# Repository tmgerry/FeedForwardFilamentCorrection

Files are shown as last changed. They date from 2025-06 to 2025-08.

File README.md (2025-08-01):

# Colorado State University - Prawel Lab

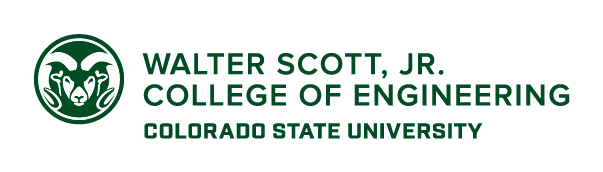
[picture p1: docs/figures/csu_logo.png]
csu logo


# Feed Forward Filament Diameter Correction

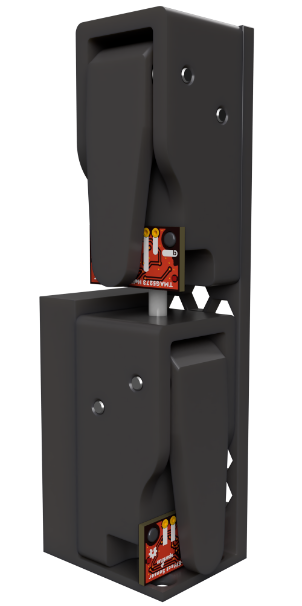
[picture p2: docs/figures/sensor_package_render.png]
diameter sensor render
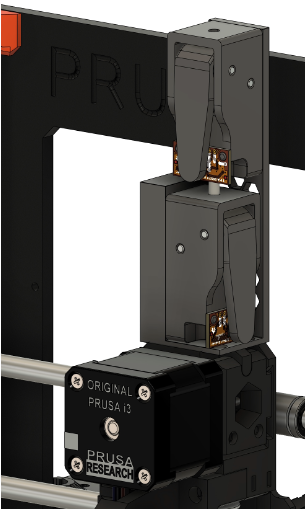
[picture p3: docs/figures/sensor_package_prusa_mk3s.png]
diameter sensor render
 

## Software Installation Instructions - 

These instructions assume you have used [Klipper Installation And Update Helper](https://github.com/dw-0/kiauh) to install klipper.

1. Clone the repository -
```
git clone https://github.com/tmgerry/FeedForwardFilamentCorrection.git
```

1. Run the install tool and restart klipper - 
```
cd && cd CSU-in-situ/ && python3 klippy/installer.py && cd && sudo service klipper restart
```

1. Configure secondary MCU and add to config based on the example configuration file.

1. Put that file in the same folder as your `printer.cfg` file.

1. Include a line like the following at the top of your existing `printer.cfg` file to activate the diameter sensor. This requires hardware and config file to be setup correctly or klipper will not start.

```
[include diameter_sensor.cfg] # Comment out if no diameter sensor is connected to disable.
```

## Microcontroller Firmware Installation

This klipper add on requires a secondary microcontroller to communicate with the magnetic sensors over I2C. This microcontroller requires klipper firmware to be installed. Other microcontrollers, (especially Sparkfun QWIIC or Adafruit Stemma QT boards, which allow for solder free wiring) are most likely compatible assuming there is a klipper firmware build compatible with the specific chip they use. The Sparkfun RP2040 Pro Micro has been extensively tested and validated to be compatible.

### Adafruit and Sparkfun RP2040 Dev Boards

Sparkfun RP2040 Pro Micro

Adafruit and Sparkfun use a different flash chip on their boards so the procedure will be the same as standard Raspberry Pi Picos except for minor setting changes in the config, and the fact that most of their boards have individual reset and boot-sel buttons.

1. Open terminal on raspberry pi with klipper installed
1. run in shell `cd klipper`
1. run in shell `make clean`
1. run in shell `make menuconfig` and the config menu will open, set the following options
   1. microcontroller architecture `Raspberry Pi RP2040`
   1. No bootloader offset
   1. Flash Chip - `GENERIC_03H with CLKDIV 4`
   1. Communication Interface - `USBSERIAL`
1. Press `Q` to save and exit
1. run in shell `make`, a bunch of lines saying "Compiling out/src......" will appear.
1. At the end you should see a line saying `Creating uf2 file out/klipper.uf2` This is the firmware file we want to upload to the pi.
1. Copy the file from above, to your computer. SFTP is convenient and easy for this.
1. Plug in the microcontroller to your computer while holding down the reset button, a removable usb-drive should appear in your file browser.
1. Drag the `klipper.uf2` file onto the picos removable drive, it will quickly disappear and restart.
1. Firmware is now flashed and the pico is ready to be used in klipper.

# Hardware

The sensor is based on the [InFiDEL Filament Diameter Sensor](https://www.printables.com/model/57154-infidel-inline-filament-diameter-estimator-lowcost), with modifications to improve accuracy and precision, as well as compatibility with TMAG5273 Hall Effect Sensor.

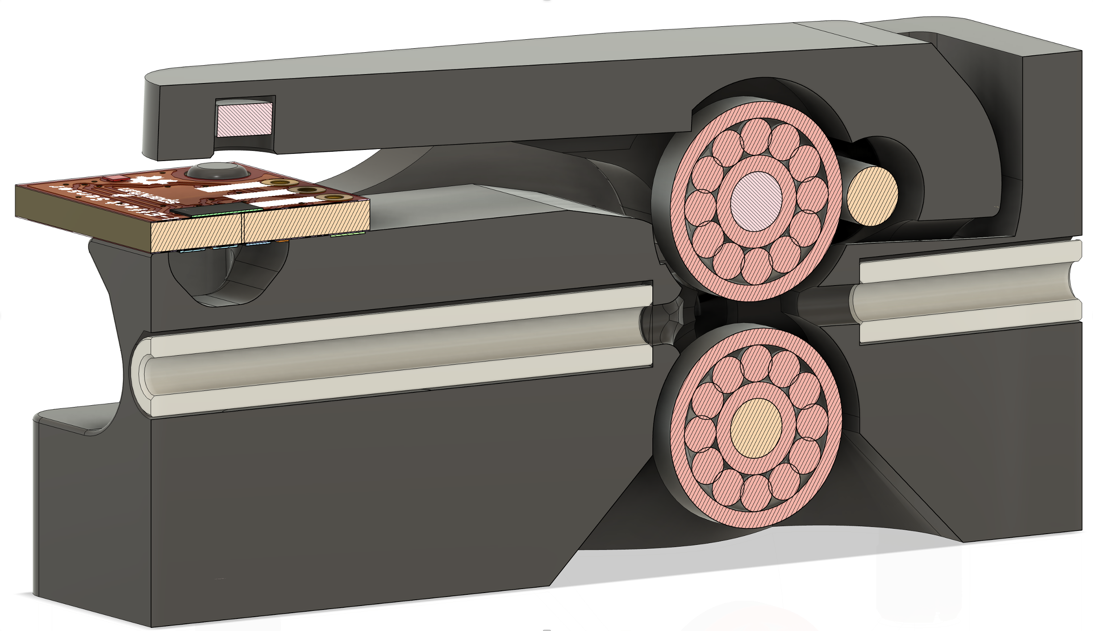
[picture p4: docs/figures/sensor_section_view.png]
sensor_section_view


## Printed Parts

There are two printed parts in this sensor, they can be printed on a standard FDM Printer, but a resin printer yields higher precision parts. We print our sensors with Formlabs Tough 1500, but stiffer materials will likely yield even better results.

The two included .STL files in the CAD folder are the ones that need to be printed.

## General BOM

* 1x Sparkfun Pro Micro RP2040 ([Sparkfun](https://www.sparkfun.com/sparkfun-pro-micro-rp2040.html))
* 1x Sparkfun QWIIC Cable Set ([Sparkfun](https://www.sparkfun.com/sparkfun-qwiic-cable-kit.html))
* Superglue for attaching the TMAG sensor.

## Sensor BOM

* (1x) Sparkfun Mini Linear 3D Hall-Effect Sensor TMAG5273 ([Sparkfun](https://www.sparkfun.com/sparkfun-mini-linear-3d-hall-effect-sensor-tmag5273-qwiic.html))
* (1x) Spring ([McMASTER-CARR](https://www.mcmaster.com/9657K629/)) *similar springs can be sourced from other vendors but we have found them to be of unreliable stiffness*
* (1x) Magnet ([McMASTER-CARR](https://www.mcmaster.com/5862K138/)) *sensor geometry is finely tuned to magnet strength, ordering this specific part is highly advised.*
* (1x) Undersized 3mm Dowel Pin 16mm Long ([McMASTER-CARR](https://www.mcmaster.com/97049A329/)) *recommend McMASTER but can be sourced other places, ensure undersized to allow for easy assembly*
* (2x) Undersized 3mm Dowel Pin 25mm Long ([Amazon](https://www.amazon.com/uxcell-Stainless-Support-Fasten-Elements/dp/B07M63LMCM?s=industrial)) *Pins in this size were harder to source, Pins from Amazon worked fine but some were not within tolerance and could not be used. They can be ordered from misumi but costs significantly more.*
* (4x) 3mmx10mmx4mm Bearings ([Amazon](https://www.amazon.com/dp/B07FW389P1?_encoding=UTF8&ref_=cm_sw_r_ud_dp_GC7XPF5W3NQKGKW1RP3B&th=1))
* (1x) M6 x 1mm Thread, 8mm Long Set Screw ([McMASTER-CARR](https://www.mcmaster.com/92605A127/))
* (4x) M3 Screw to Expand Inserts. ([McMASTER-CARR](https://www.mcmaster.com/94510A030/)) *for rear sensor mounting holes, only necesarry if there is frequent assembly/dissassembly*
* Calibration Hardware

## Sensor Calibration

The filament diameter sensor can only be as accurate as it's calibration. We use a 3 point calibration with the pin gauges featured below to calibrate the sensor, a more extensive calibration could be done with four, five, or even 6+ pins to make it more precise but 3 was chosen by our team to have the optimal balance of cost, time, and accuracy.

### Calibration Gauges

* (1x) 0.0665 Class Z No Go Gauge ([McMASTER-CARR](https://www.mcmaster.com/23065A674-23065A305/))
* (1x) 0.0690 Class Z No Go Gauge ([McMASTER-CARR](https://www.mcmaster.com/23065A674-23065A069/))
* (1x) 0.0710 Class Z No Go Gauge ([McMASTER-CARR](https://www.mcmaster.com/23065A674-23065A071/))

### Calibration Procedure

1. Using the microcontroller selected above - flash the calibration firmware using the inlcuded arduino sketch.
   1. Ensure to set the i2c address at the top of the file to the appropriate sensor if using a dual sensor configuration.
1. Place calibration gauge into sensor from the TMAG side
1. Open Arduino serial console and clear output
1. Log as many values as you want and store in a spreadsheet
1. Repeat for each calibration pin you have.
1. Run a linear regression on the samples you collected to get the correct calibration values to input into your config file.

# Klipper Configuration
[Example configuration available here](config_examples/diameter_sensor_example.cfg)

# More Info

### How extrusion is changed -

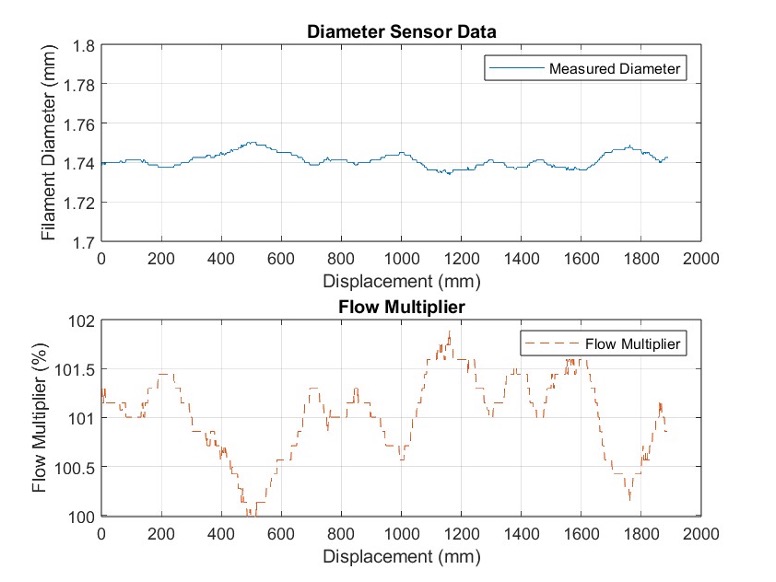
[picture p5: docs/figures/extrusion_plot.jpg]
extrusion plot

*Simple plot showing how changes in filament diameter change the klipper extrusion multiplier*

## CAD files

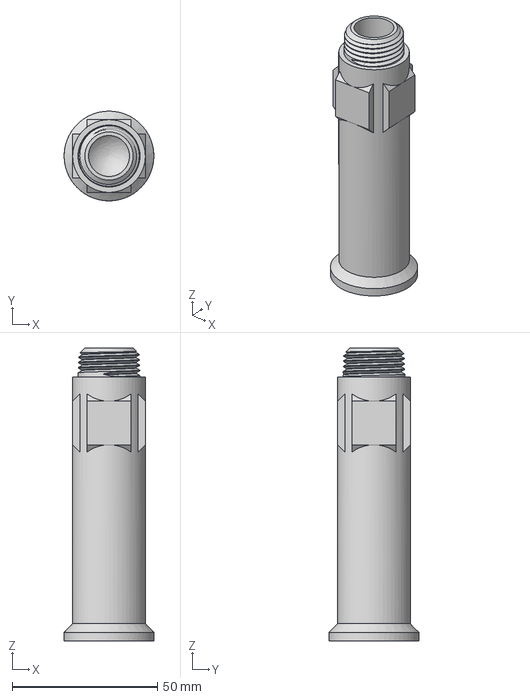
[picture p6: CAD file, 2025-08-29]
CAD/pressure_tube/tube_042.step
30.9 x 30.9 x 100.8 mm

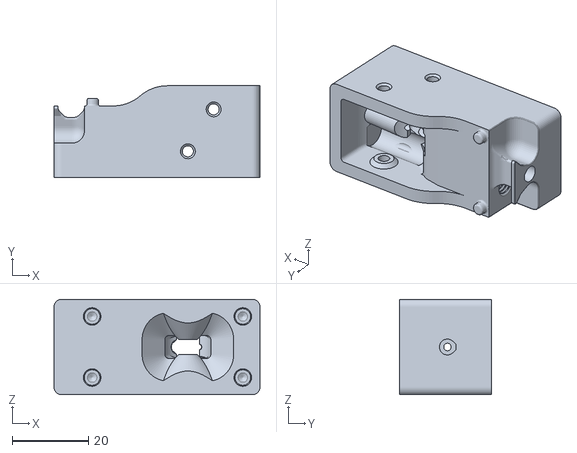
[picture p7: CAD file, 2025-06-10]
CAD/Sensor_Body.stl
54.0 x 24.0 x 25.0

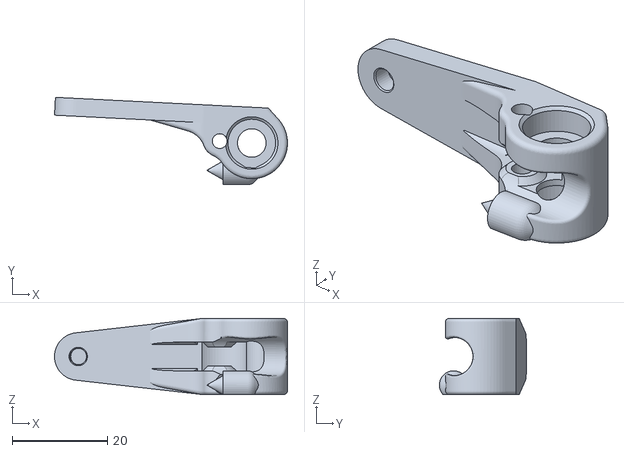
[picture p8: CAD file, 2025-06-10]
CAD/Lever.stl
48.9 x 18.3 x 16.0

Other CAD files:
CAD/Filament Diameter Sensor.f3d

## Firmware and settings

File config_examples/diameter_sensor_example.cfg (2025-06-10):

# Include the following line in your printer.cfg file
#
# [include diameter_sensor.cfg] # comment out if no diameter sensor is connected
# 

[mcu diameter_sensor_mcu]
serial: /dev/serial/by-id/usb-Klipper_rp2040..............

[tmag5273_filament_width_sensor]
i2c_mcu: diameter_sensor_mcu
i2c_bus: i2c0e
i2c_speed: 100000
# Calibration
cal_slope_1: -1.385324e-05  # Sensor 0
cal_intercept_1: 2.069541   # Sensor 0	

cal_slope_2: -1.374351e-05  # Sensor 1
cal_intercept_2: 2.067393   # Sensor 1

#   The nominal filament diameter. This parameter must be provided.
default_nominal_filament_diameter: 1.75
max_difference: 100
#   Maximum allowed filament diameter difference in millimeters (mm).
#   If difference between nominal filament diameter and sensor output
#   is more than +- max_difference, extrusion multiplier is set back
#   to %100. The default is 0.200.
measurement_delay_1: 147.5
measurement_delay_2: 203
#   The distance from sensor to the melting chamber/hot-end in
#   millimeters (mm). The filament between the sensor and the hot-end
#   will be treated as the default_nominal_filament_diameter.
enable: False
#   Sensor enabled or disabled after power on. The default is to
#   disable.
# measurement_interval: 2
#   The approximate distance (in mm) between sensor readings. The
#   default is 2mm.
# logging: True
#   Out diameter to terminal and klipper.log can be turn on|of by
#   command.
min_diameter: 0
#   Minimal diameter for trigger virtual filament_switch_sensor.
max_diameter: 100
#   Maximum diameter for triggering virtual filament_switch_sensor.
#   The default is default_nominal_filament_diameter + max_difference.
use_current_dia_while_delay: False
#   Use the current diameter instead of the nominal diameter while
#   the measurement delay has not run through.
average_mode: 5
z_axis_range_80mT: False
xy_axis_range_80mT: False
super_sampling: 75
mag_temp_mode: 0
dual_sensor: True


[temperature_sensor diameter_sensor_CPU]
sensor_type: temperature_mcu
sensor_mcu: diameter_sensor_mcu
min_temp: -10
max_temp: 100


[temperature_sensor diameter_sensor_1]
sensor_type: TMAG5273_TEMP
tmag_poll_time: 1
sensor_number: 1

[temperature_sensor diameter_sensor_2]
sensor_type: TMAG5273_TEMP
tmag_poll_time: 1
sensor_number: 2



[gcode_macro disable_filament_correction]
gcode:
    M221 S10
    DISABLE_FILAMENT_WIDTH_SENSOR
    RESET_FILAMENT_WIDTH_SENSOR
    SET_LED LED=sensor_status RED=1 GREEN=0 BLUE=0

[gcode_macro enable_filament_correction]
gcode:
   ENABLE_FILAMENT_WIDTH_SENSOR
   SET_LED LED=sensor_status RED=0 GREEN=1 BLUE=1

[gcode_macro get_filament_width]
gcode:
    QUERY_FILAMENT_WIDTH
    QUERY_RAW_FILAMENT_WIDTH

[gcode_macro _reset_filament_width]
gcode:
    RESET_FILAMENT_WIDTH_SENSOR


[gcode_macro get_filament_sensor_temps]
gcode:
    GET_FILAMENT_WIDTH_SENSOR_TEMPS


[gcode_macro get_filament_sensor_debug]
gcode:
  GET_FILAMENT_WIDTH_SENSOR_DEBUG

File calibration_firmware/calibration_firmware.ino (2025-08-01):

#include <Wire.h>      // Used to establish serial communication on the I2C bus
#include "tmag_5273.h" // Used to send and recieve specific information from our sensor

TMAG5273 sensor; // Initialize hall-effect sensor

// I2C default address
// Alternate i2c address comments to switch between sensors when using more than 1 sensor
// uint8_t i2cAddress = 0x78;
uint8_t i2cAddress = 0x22;

int super_sample = 250;
float z_buffer = 0;

void setup() 
{
  Wire.begin();
  // Start serial communication at 115200 baud
  Serial.begin(115200);
  delay(1000);

  // Begin example of the magnetic sensor code (and add whitespace for easy reading)
  Serial.println("TMAG5273 Example 1: Basic Readings");
  Serial.println("");

  // If begin is successful (0), then start example
  if(sensor.begin(i2cAddress, Wire) == 1)
  {
    Serial.println("Begin");
  }
  else // Otherwise, infinite loop
  {
    Serial.println("Device failed to setup - Freezing code.");
    // while(1); // Runs forever
  }
  sensorSetup();
}


void loop() 
{
  // Checks if mag channels are on - turns on in setup
  if(sensor.getMagneticChannel() != 0) 
  {
    sensor.setTemperatureEn(true);

    // float magX = sensor.getXData();
    // float magY = sensor.getYData();
    z_buffer = 0;
    for (int i = 0; i < super_sample; i++) {
      float magZ = sensor.getZDataRaw();
      // magZ = ((magZ/80*32768)*-0.0000157091914)+1.998755832;
      z_buffer += magZ;
    }
    z_buffer = z_buffer / super_sample;
    Serial.println(z_buffer, 5);
  }
  else
  {
    // If there is an issue, stop the magnetic readings and restart sensor/example
    Serial.println("Mag Channels disabled, stopping..");
    while(1);
  }

  delay(100);
}



void sensorSetup(){
  Serial.print("Averaging Mode: ");
  Serial.println(sensor.getConvAvg());
  sensor.setConvAvg(0X5);
  delay(500);
  Serial.print("Read Mode Set: ");
  Serial.println(sensor.setReadMode(0X0));
  sensor.setMagneticChannel(0X4);
  sensor.setLowPower(0X1);
  sensor.setGlitchFilter(0X0);
  delay(500);
  sensor.setZAxisRange(0X0);
  delay(500);
  sensor.setMagTemp(0x1);
  delay(1000);
  Serial.print("Averaging Mode: ");
  Serial.println(sensor.getConvAvg());
  Serial.print("Read Mode: ");
  Serial.println(sensor.getReadMode());
  Serial.print("Power Mode: ");
  Serial.println(sensor.getLowPower());
  Serial.print("Range: ");
  Serial.println(sensor.getZAxisRange());
  Serial.print("Temp Mode: ");
  Serial.println(sensor.getMagTemp());
  Serial.print("Glitch Filter: ");
  Serial.println(sensor.getGlitchFiler());
}

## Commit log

2025-06-10 Added Files modified: .gitignore new file: CAD/Filament Diameter Sensor.f3d new file: CAD/Lever.stl new file: CAD/Sensor_Body.stl modified: README.md new file: config_examples/diameter_sensor_example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
    [Filament Diameter Sensor.f3d, Lever.stl, Sensor_Body.stl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]
2025-08-01 Updates to Documentation - Added Figures modified: .gitignore modified: README.md new file: calibration_firmware/calibration_firmware.ino new file: calibration_firmware/tmag_5273.cpp new file: calibr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
2025-08-28 Added Pressure Test Sample STL
2025-08-29 Added step file and made pressure_tube cad folder new file: CAD/pressure_tube/tube_042.step renamed: CAD/tube_042.stl -> CAD/pressure_tube/tube_042.stl
    [tube_042.step]
